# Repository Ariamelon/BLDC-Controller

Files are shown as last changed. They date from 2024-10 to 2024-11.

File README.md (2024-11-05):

# BLDC motor controller
A brushless DC motor controller developed in partial fulfilment of the requirements for a degree of BEng (Hons) Electronic & Computer Engineering.

## Disclaimer
The hardware is licensed under CERN-OHL-S-2.0, and the firmware is licensed under GNU GPLv3. 

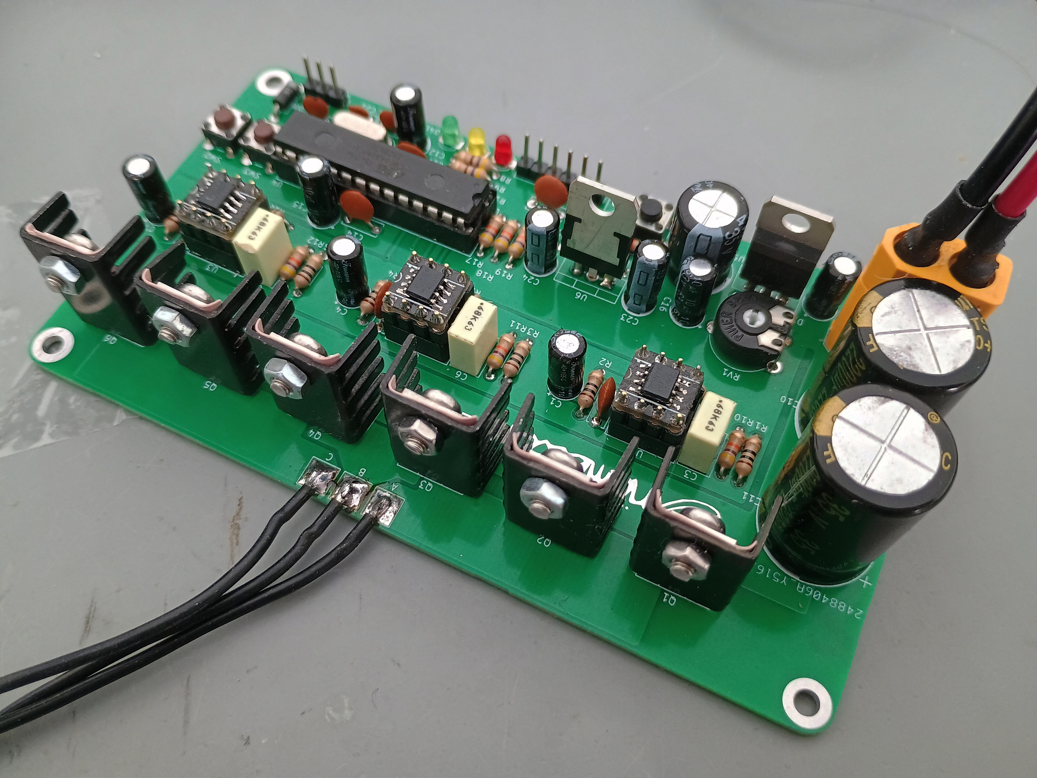
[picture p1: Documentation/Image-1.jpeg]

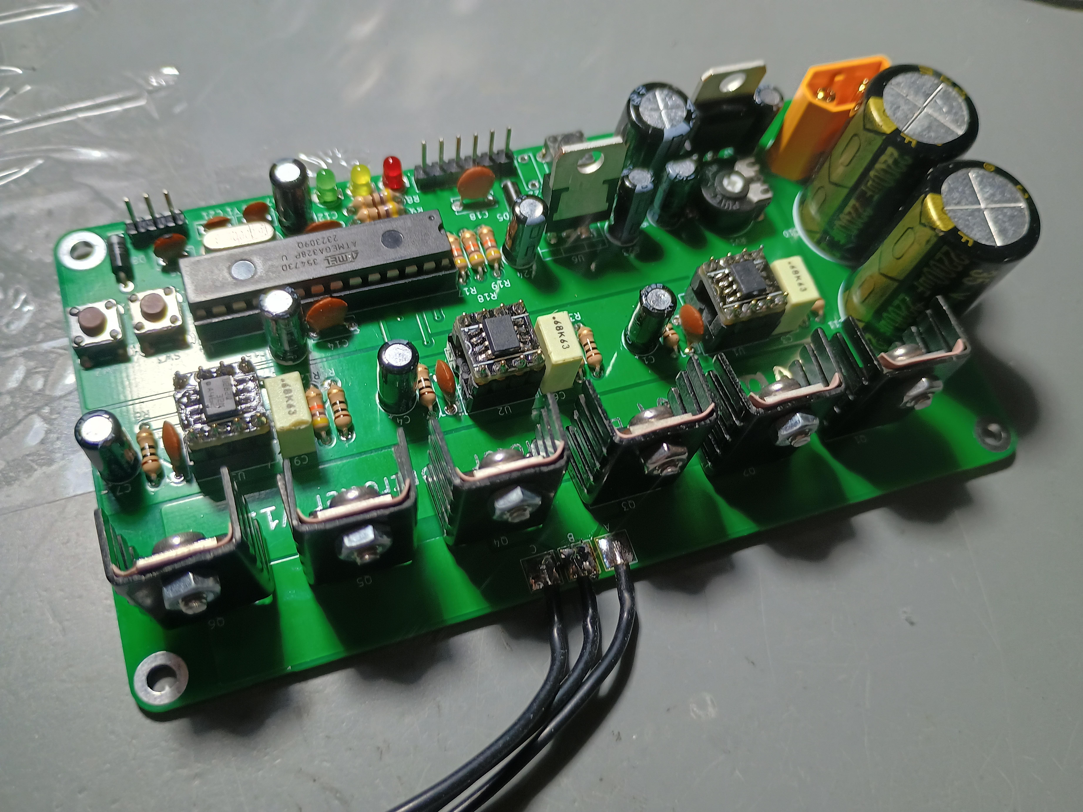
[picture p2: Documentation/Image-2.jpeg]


https://github.com/user-attachments/assets/5595b5e6-1121-481e-8a8e-658866d14e04

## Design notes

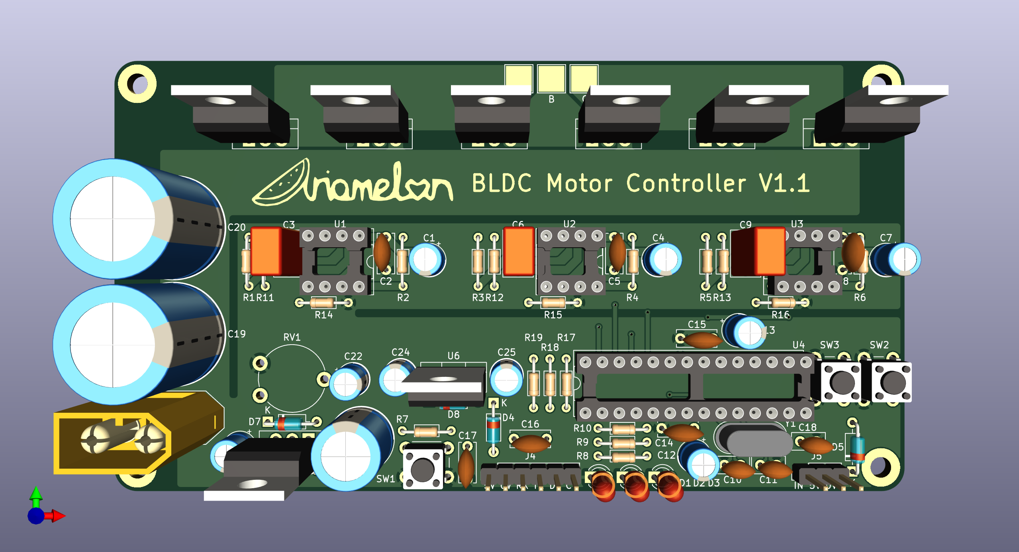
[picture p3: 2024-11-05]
Documentation/BLDC-Controller-3D.png

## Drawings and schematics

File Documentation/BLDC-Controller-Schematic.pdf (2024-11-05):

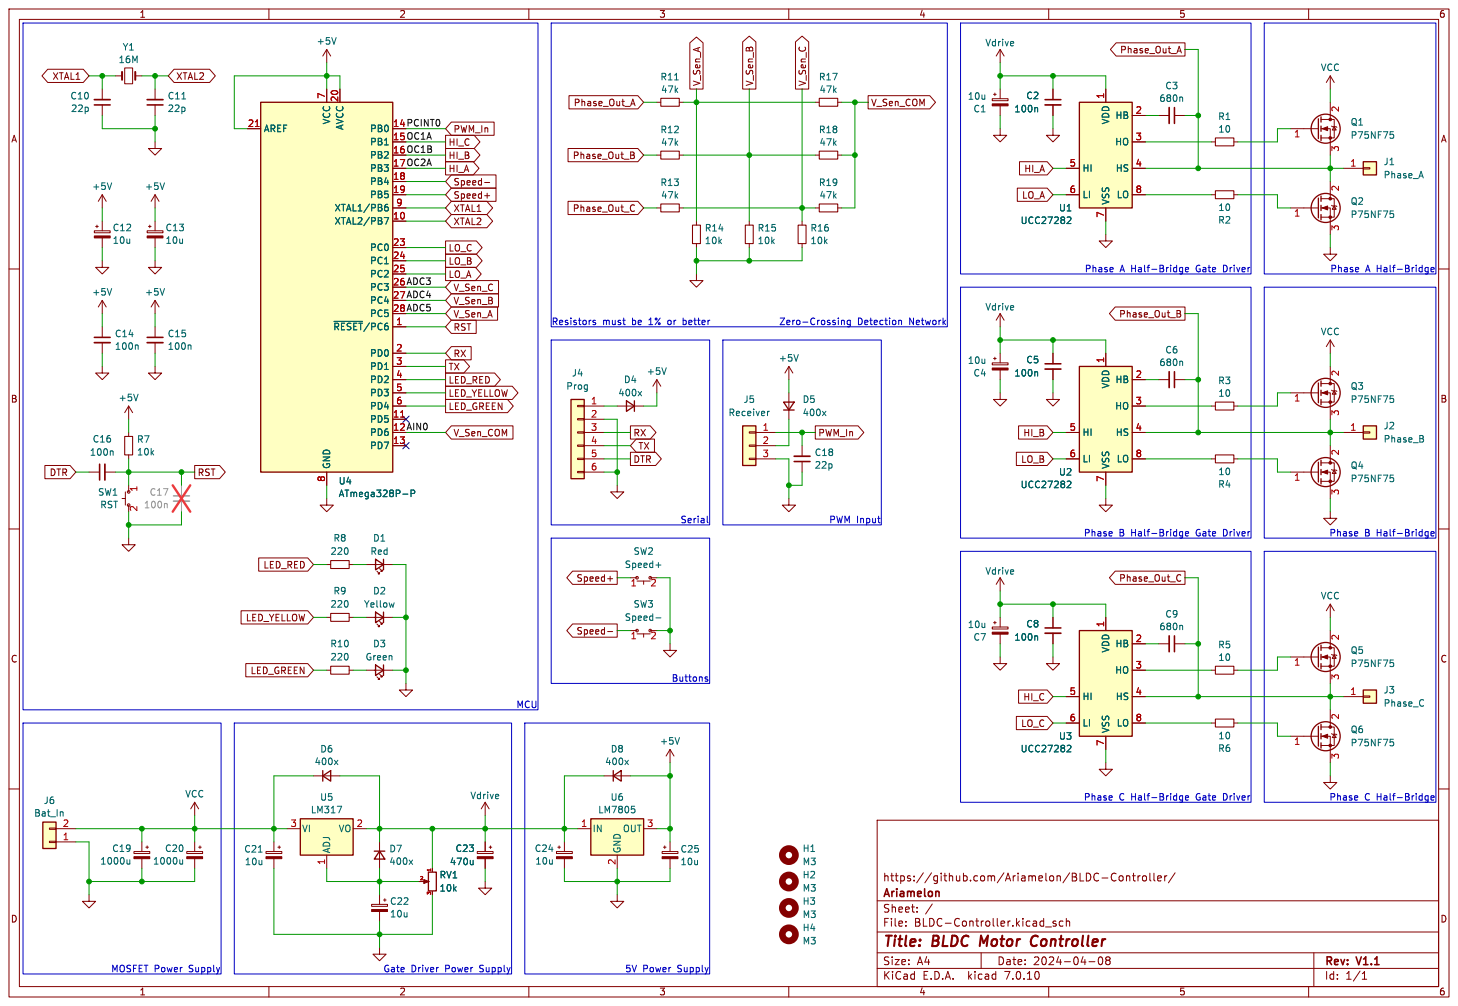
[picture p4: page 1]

https://github.com/Ariamelon/BLDC-Controller/
Id: 1/1 Title: BLDC Motor Controller File: BLDC-Controller.kicad_sch Sheet: / Ariamelon

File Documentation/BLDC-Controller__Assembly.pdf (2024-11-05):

# A CT C

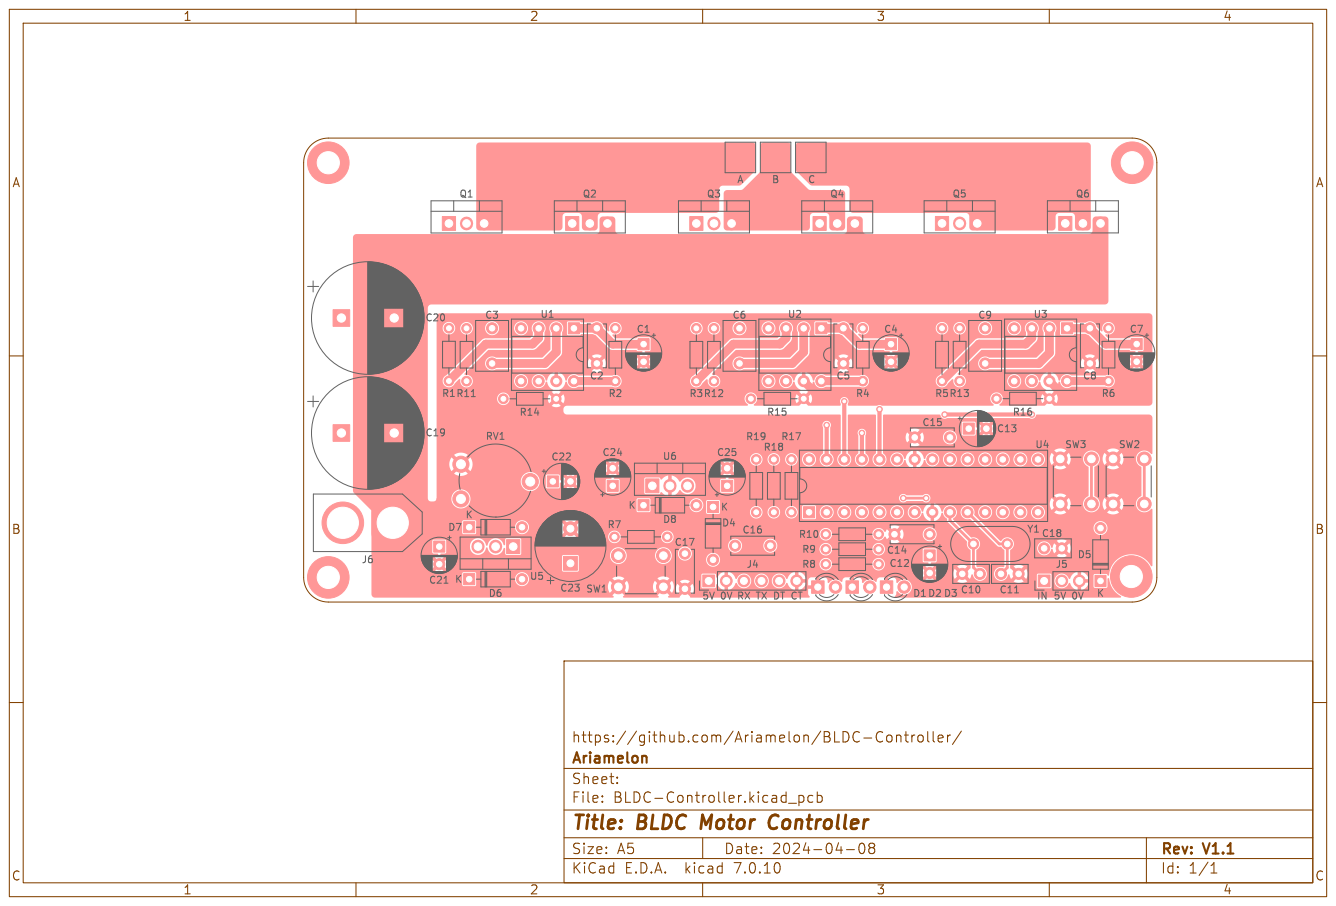
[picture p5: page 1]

https://github.com/Ariamelon/BLDC-Controller/

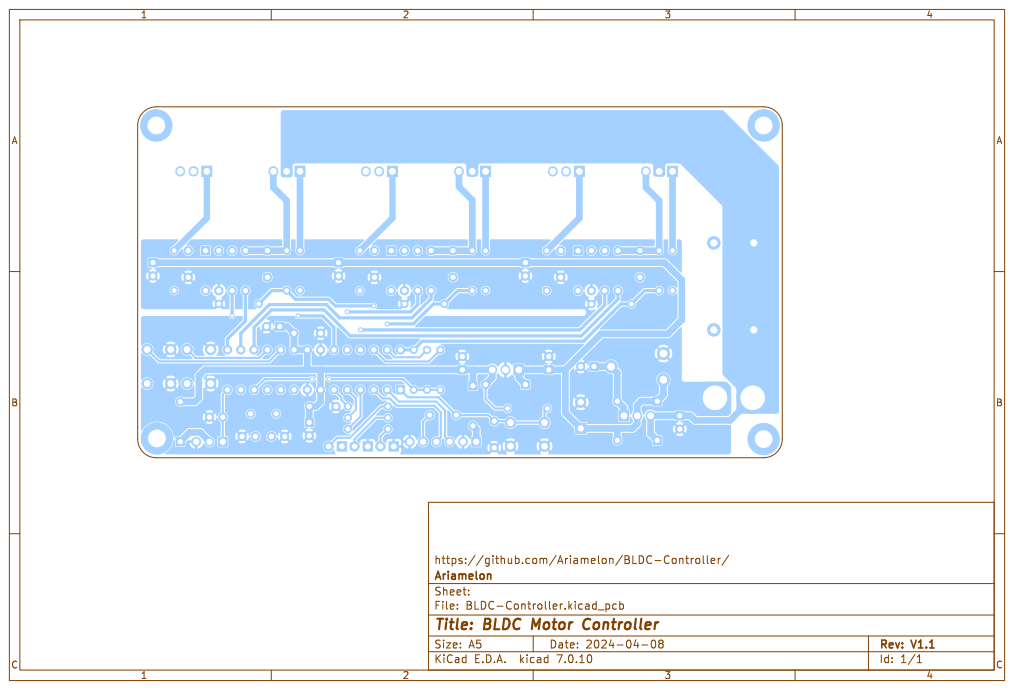
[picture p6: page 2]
BC Date: 2024-04-08 KiCad; kicad; 7.0.10 Size: A5; Rev: V1.1; Id: 1/1 Title: BLDC Motor Controller File:; BLDC-Controller.kicad_pcb Sheet: Ariamelon

https://github.com/Ariamelon/BLDC-Controller/

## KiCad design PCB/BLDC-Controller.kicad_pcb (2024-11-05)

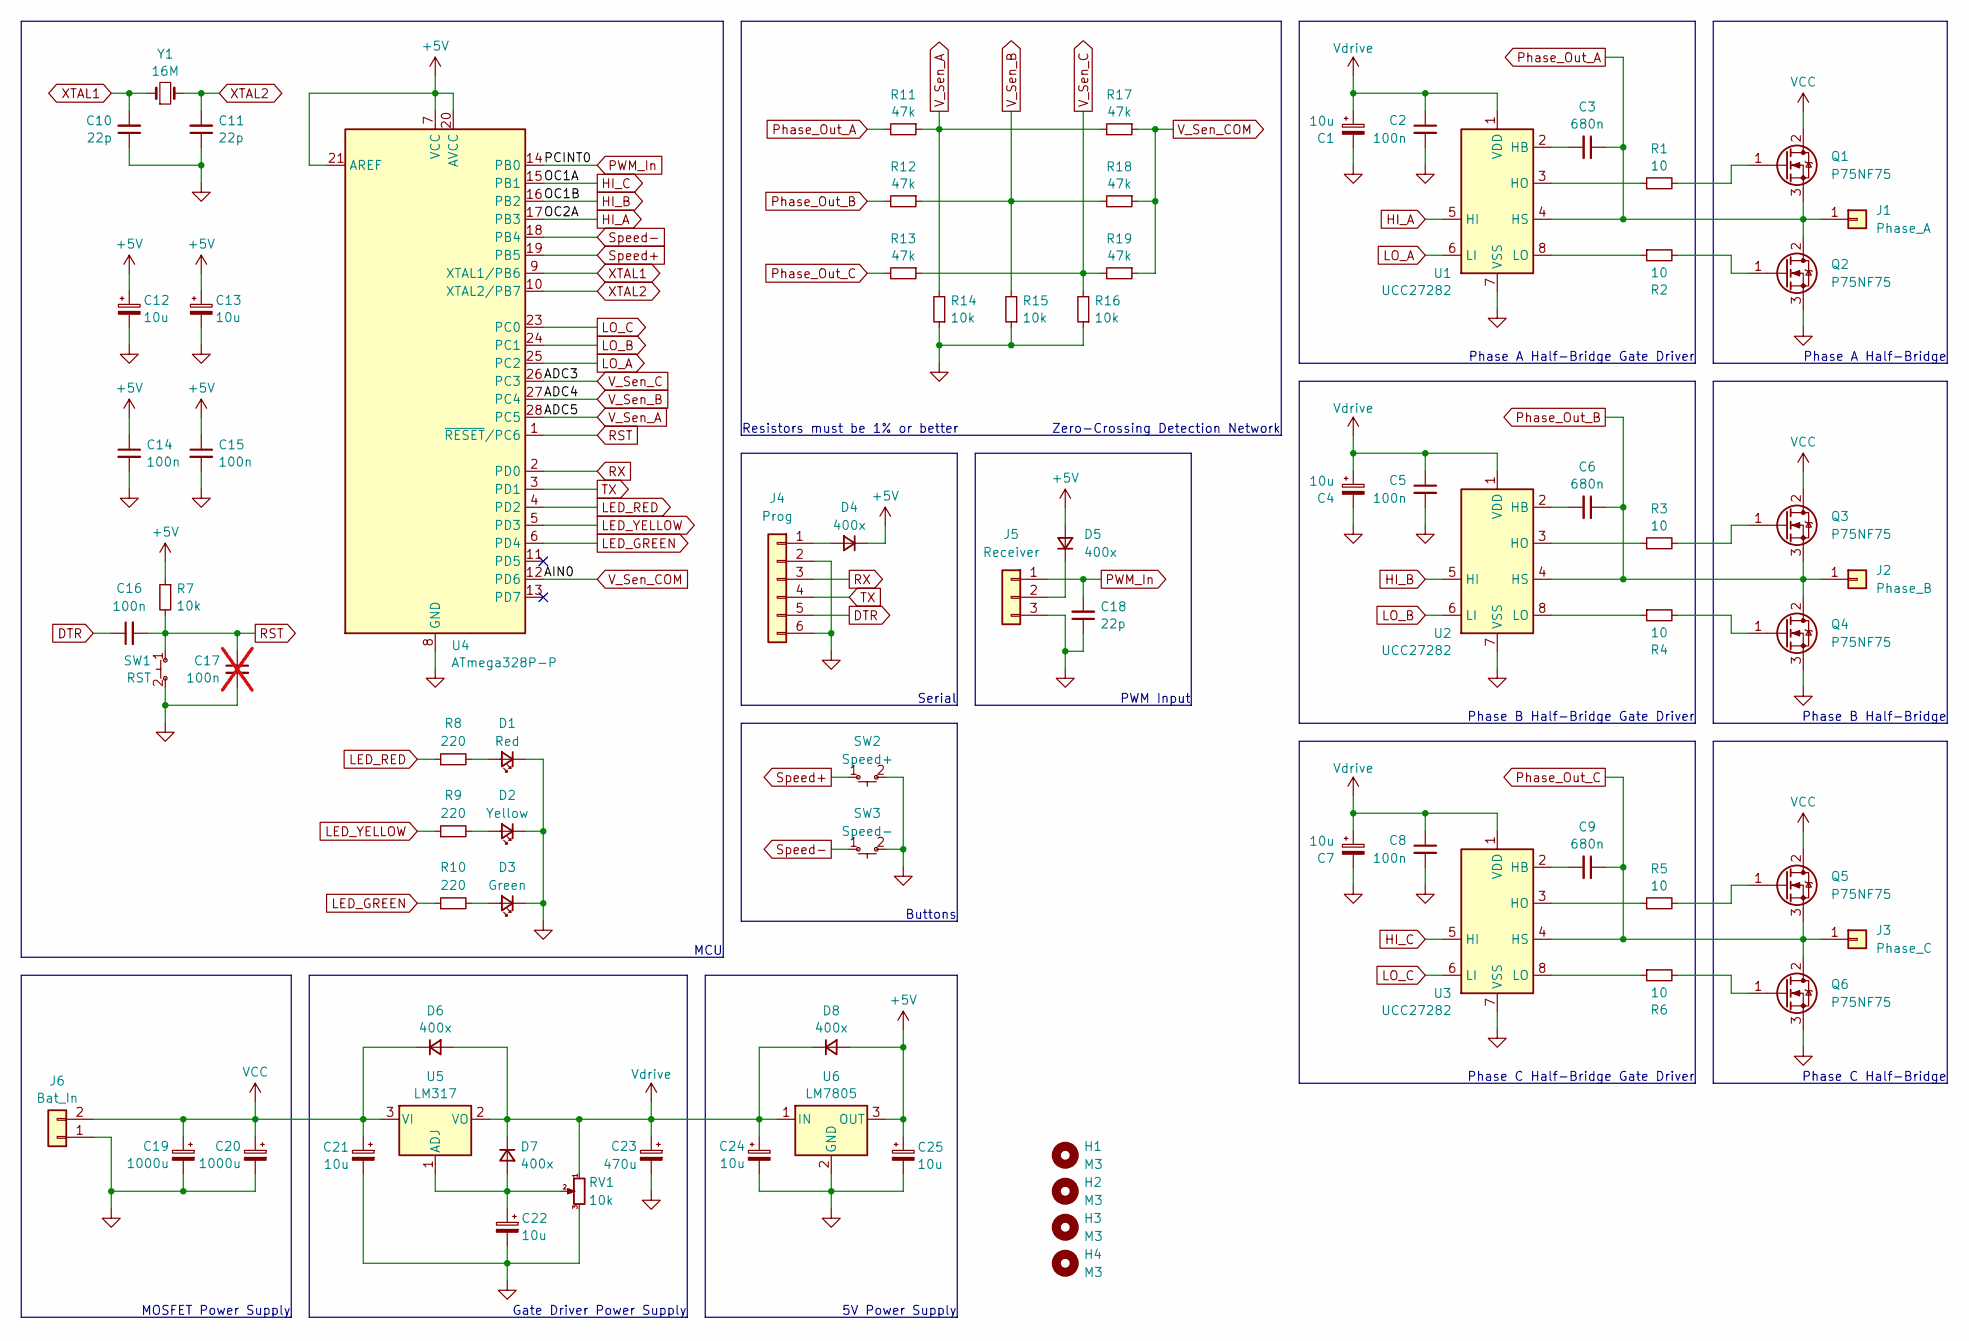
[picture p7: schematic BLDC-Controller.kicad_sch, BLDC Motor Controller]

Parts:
C1, C4, C7, C12, C13, C21, C22, C24, C25: 10u; CP_Radial_D5.0mm_P2.54mm
C2, C5, C8, C14, C15, C16: 100n; C_Disc_D6.0mm_W2.5mm_P5.08mm
C3, C6, C9: 680n; C_Rect_L7.0mm_W4.5mm_P5.08mm
C10, C11, C18: 22p; C_Disc_D5.0mm_W2.5mm_P2.54mm
C17: 100n; C_Disc_D6.0mm_W2.5mm_P5.08mm; not fitted
C19, C20: 1000u; CP_Radial_D16.0mm_P7.62mm
C23: 470u; CP_Radial_D10.0mm_P5.00mm
D1: Red; LED_D3.0mm
D2: Yellow; LED_D3.0mm
D3: Green; LED_D3.0mm
D4, D5, D6, D7, D8: 400x; D_DO-35_SOD27_P7.62mm_Horizontal
H1, H2, H3, H4: M3; MountingHole_3.2mm_M3_Pad
J1: Phase_A; TestPoint_Pad_4.0x4.0mm
J2: Phase_B; TestPoint_Pad_4.0x4.0mm
J3: Phase_C; TestPoint_Pad_4.0x4.0mm
J4: Prog; PinHeader_1x06_P2.54mm_Vertical
J5: Receiver; PinHeader_1x03_P2.54mm_Vertical
J6: Bat_In; AMASS_XT60-M_1x02_P7.20mm_Vertical
Q1, Q2, Q3, Q4, Q5, Q6: P75NF75; TO-220-3_Vertical
R1, R2, R3, R4, R5, R6: 10; R_Axial_DIN0204_L3.6mm_D1.6mm_P7.62mm_Horizontal
R7, R14, R15, R16: 10k; R_Axial_DIN0204_L3.6mm_D1.6mm_P7.62mm_Horizontal
R8, R9, R10: 220; R_Axial_DIN0204_L3.6mm_D1.6mm_P7.62mm_Horizontal
R11, R12, R13, R17, R18, R19: 47k; R_Axial_DIN0204_L3.6mm_D1.6mm_P7.62mm_Horizontal
RV1: 10k; Potentiometer_Piher_PT-10-V10_Vertical
SW1: RST; SW_PUSH_6mm
SW2: Speed+; SW_PUSH_6mm
SW3: Speed-; SW_PUSH_6mm
U1, U2, U3: UCC27282; DIP-8_W7.62mm_Socket
U4: ATmega328P-P; DIP-28_W7.62mm_Socket
U5: LM317; TO-220-3_Vertical
U6: LM7805; TO-220-3_Vertical
Y1: 16M; Crystal_HC49-4H_Vertical

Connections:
+5V: C12.1, C13.1, C14.1, C15.1, C25.1, D4.1 (K), D5.2 (A), D8.2 (A), R7.1, U4.7 (VCC), U4.20 (AVCC), U4.21 (AREF), U6.3 (OUT)
DTR: C16.1, J4.5
GND: C1.2, C2.2, C4.2, C5.2, C7.2, C8.2, C10.1, C11.1, C12.2, C13.2, C14.2, C15.2, C17.2, C18.1, C19.2, C20.2, C21.2, C22.2, C23.2, C24.2, C25.2, D1.1 (K), D2.1 (K), D3.1 (K), J4.2, J4.6, J5.3, J6.1, Q2.3 (S), Q4.3 (S), Q6.3 (S), R14.1, R15.1, R16.1, RV1.3, SW1.2 (B), SW2.2 (B), SW3.2 (B), U1.7 (VSS), U1.9 (EP), U2.7 (VSS), U2.9 (EP), U3.7 (VSS), U3.9 (EP), U4.8 (GND), U4.22 (GND), U6.2 (GND)
HI_A: U1.5 (HI), U4.17 (PB3)
HI_B: U2.5 (HI), U4.16 (PB2)
HI_C: U3.5 (HI), U4.15 (PB1)
LED_GREEN: R10.1, U4.6 (PD4)
LED_RED: R8.1, U4.4 (PD2)
LED_YELLOW: R9.1, U4.5 (PD3)
LO_A: U1.6 (LI), U4.25 (PC2)
LO_B: U2.6 (LI), U4.24 (PC1)
LO_C: U3.6 (LI), U4.23 (PC0)
unnamed: D1.2 (A), R8.2
unnamed: D2.2 (A), R9.2
unnamed: D3.2 (A), R10.2
unnamed: D4.2 (A), J4.1
unnamed: D5.1 (K), J5.2
unnamed: C22.1, D7.2 (A), RV1.2, U5.1 (ADJ)
unnamed: Q1.1 (G), R1.2
unnamed: Q2.1 (G), R2.2
unnamed: Q3.1 (G), R3.2
unnamed: Q4.1 (G), R4.2
unnamed: Q5.1 (G), R5.2
unnamed: Q6.1 (G), R6.2
unnamed: C3.2, U1.2 (HB)
unnamed: R1.1, U1.3 (HO)
unnamed: R2.1, U1.8 (LO)
unnamed: C6.2, U2.2 (HB)
unnamed: R3.1, U2.3 (HO)
unnamed: R4.1, U2.8 (LO)
unnamed: C9.2, U3.2 (HB)
unnamed: R5.1, U3.3 (HO)
unnamed: R6.1, U3.8 (LO)
PWM_In: C18.2, J5.1, U4.14 (PB0)
Phase_Out_A: C3.1, J1.1, Q1.3 (S), Q2.2 (D), R11.2, U1.4 (HS)
Phase_Out_B: C6.1, J2.1, Q3.3 (S), Q4.2 (D), R12.2, U2.4 (HS)
Phase_Out_C: C9.1, J3.1, Q5.3 (S), Q6.2 (D), R13.2, U3.4 (HS)
RST: C16.2, C17.1, R7.2, SW1.1 (A), U4.1 (~RESET/PC6)
RX: J4.3, U4.2 (PD0)
Speed+: SW2.1 (A), U4.19 (PB5)
Speed-: SW3.1 (A), U4.18 (PB4)
TX: J4.4, U4.3 (PD1)
VCC: C19.1, C20.1, C21.1, D6.1 (K), J6.2, Q1.2 (D), Q3.2 (D), Q5.2 (D), U5.3 (VI)
V_Sen_A: R11.1, R14.2, R17.2, U4.28 (PC5)
V_Sen_B: R12.1, R15.2, R18.2, U4.27 (PC4)
V_Sen_C: R13.1, R16.2, R19.2, U4.26 (PC3)
V_Sen_COM: R17.1, R18.1, R19.1, U4.12 (PD6)
Vdrive: C1.1, C2.1, C4.1, C5.1, C7.1, C8.1, C23.1, C24.1, D6.2 (A), D7.1 (K), D8.1 (K), RV1.1, U1.1 (VDD), U2.1 (VDD), U3.1 (VDD), U5.2 (VO), U6.1 (IN)
XTAL1: C10.2, U4.9 (XTAL1/PB6), Y1.1
XTAL2: C11.2, U4.10 (XTAL2/PB7), Y1.2

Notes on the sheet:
MOSFET Power Supply
Gate Driver Power Supply
Resistors must be 1% or better
5V Power Supply
PWM Input
Buttons
Phase A Half-Bridge Gate Driver
Serial
Zero-Crossing Detection Network
Phase C Half-Bridge Gate Driver
Phase C Half-Bridge
Phase A Half-Bridge
Phase B Half-Bridge
Phase B Half-Bridge Gate Driver
MCU

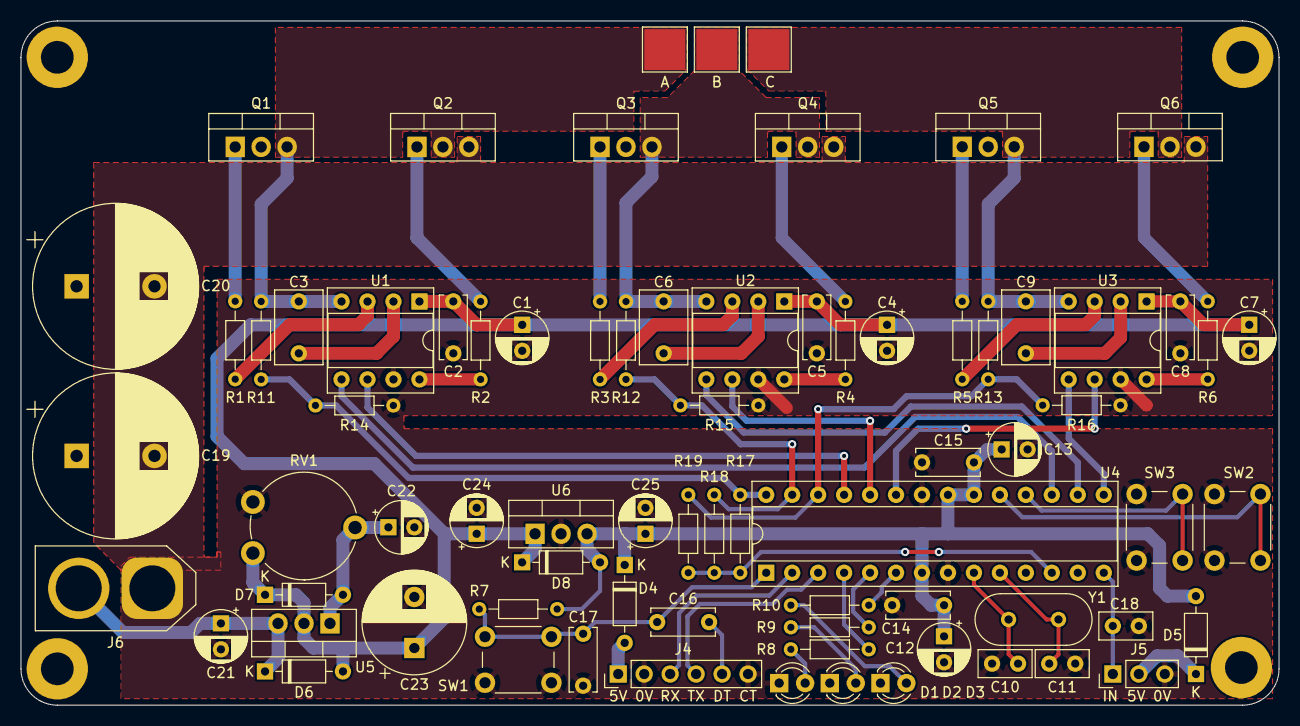
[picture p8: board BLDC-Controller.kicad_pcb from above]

Board: 2 copper layers, 123.1 x 66.9 mm, 80 parts (0 on the bottom side), 50 nets.

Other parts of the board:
A1: Art; Ariamelon_Logo_Large_Mask

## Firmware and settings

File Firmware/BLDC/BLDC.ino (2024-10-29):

/*
This file is part of BLDC control firmware.

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
You should have received a copy of the GNU General Public License along with BLDC control firmware.
If not, see <https://www.gnu.org/licenses/>. 
*/

#include <stdlib.h>
#include "Commutation.h"
#include "UART_Comms.h"

static volatile unsigned char commutation_step = 0;

// Analog comparator ISR
ISR (ANALOG_COMP_vect) {
  unsigned char i;

  // Debouncing filter. Reads values DEBOUNCE_PERIOD times before processing result.
  // Increases debounce period if BLDC step is odd & 0 detected on ACO (comparator output).
  // Or if BLDC step is even & 1 detected on ACO (comparator output).
  for(i = 0; i < DEBOUNCE_PERIOD; i++) {
    if(((commutation_step & 1) && !(ACSR & 0b00100000)) 
   || (!(commutation_step & 1) && (ACSR & 0b00100000))){
      i -= 1;
    }
  }

  commutation_step = commutation_step_set(commutation_step);
}

int main(void){
  init();
  
  Serial.begin(BAUD);
  while(Serial.available() > 0){
    Serial.read();
  }
  Serial.flush();
  
  Serial.println("Initializing BLDC motor controller.");
  initialize_controller();
  Serial.println("Initialization complete.");

  // Speed control via on-board buttons or serial input.
  // Some Arduino functions used here as speed is not critical.

  unsigned char pwm_old_duty = 0;
  unsigned char pwm_min_duty = 65 - VOLTAGE_IN * 2;
  int pwm_new_duty = 0;
  char uart_buffer[UART_BUFFER_SIZE];
  bool motor_spinning = 0;

  while(1){
    while(Serial.available() > 0){
      if(!UART_process_data(uart_buffer, UART_BUFFER_SIZE)){
        pwm_new_duty = strtoul(uart_buffer, NULL, 0);
      }
    }

    if(!(PINB & (1 << PINB5))){             // Speed up button pressed.
      pwm_new_duty++;
      delay(10);
    }

    else if(!(PINB & (1 << PINB4))){        // Speed down button pressed.
      pwm_new_duty--;
      delay(10);
    }

    if (pwm_new_duty < pwm_min_duty){
      if (pwm_new_duty > pwm_old_duty){     // Constrain lower limit.
        pwm_new_duty = pwm_min_duty;        // Interpret as motor start command.
      }
      else{
        pwm_new_duty = 0;                   // Interpret as motor stop command.
      }
    }
    else if (pwm_new_duty > PWM_MAX_DUTY){  // Constrain upper limit.
      pwm_new_duty = PWM_MAX_DUTY;
    }

    if (pwm_new_duty != pwm_old_duty){      // Ignore command if value is unchanged.
      if (pwm_new_duty == 0){
        motor_stop();
      }
      else if (pwm_old_duty == 0){          // If motor is stationary, any number starts the motor.
        pwm_new_duty = pwm_min_duty;
        commutation_step = motor_start(pwm_new_duty, commutation_step, VOLTAGE_IN);
      }
      Serial.print("Duty cycle: ");
      Serial.print(pwm_new_duty);
      Serial.println("/255.");

      pwm_duty_set(pwm_new_duty);
      pwm_old_duty = pwm_new_duty;
    }
  }  
}

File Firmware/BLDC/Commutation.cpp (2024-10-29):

/*
This file is part of BLDC control firmware.

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
You should have received a copy of the GNU General Public License along with BLDC control firmware.
If not, see <https://www.gnu.org/licenses/>. 
*/

#include "Arduino.h"
#include "Commutation.h"

void initialize_controller(void){
  DDRB   |= 0b00001110; // Configure HI_A (PB3), HI_B (PB2) and HI_C (PB1) (high side) as outputs.
  PORTB  &= 0b11110001; // Disable HI_A (PB3), HI_B (PB2) and HI_C (PB1).
  PORTB  |= 0b00110000; // Enable speed+ (PB5) and speed- (PB4) pullups.

  DDRC   |= 0b00000111; // Configure LO_A (PC2), LO_B (PC1) and LO_C (PC0) (low side) as outputs.
  PORTC  &= 0b11111000; // Disable LO_A (PC2), LO_B (PC1) and LO_C (PC0).
  
  DDRD   |= 0b00011100; // Configure red LED (PD2), yellow LED (PD3) and green LED (PD4) as outputs.
  PORTD  &= 0b11100111; // Disable yellow LED (PD3) and green LED (PD4).
  PORTD  |= 0b00000100; // Enable red LED (PD2).

  TCCR1A  = 0;          // Initialize timers 1 and 2.
  TCCR1B  = 0b00000001; // Clock source set to clkIO / 1 (no prescaling).
  TCCR2A  = 0;          // Allows for highest PWM frequency.
  TCCR2B  = 0b00000001; // Also disable PWM outputs.

  ACSR    = 0b00010000; // Disable and clear ACI flag (analog comparator interrupt).
  ADCSRA  = 0;          // Disable ADC.
}

unsigned char motor_start(unsigned char pwm_lowest_duty, unsigned char old_step, unsigned char input_voltage){
  Serial.print("Starting up motor. ");
  PORTD |= 0b00001000;  // Enable yellow LED (PD3).

  // Acceleration rate depends on duty cycle and input voltage.
  unsigned int delay_duration = OPEN_LOOP_DELAY;
  unsigned int delay_factor = 70;
  unsigned char pwm_start_duty = delay_factor - input_voltage;

  pwm_duty_set(pwm_start_duty);
  unsigned char new_step = old_step;

  new_step = commutation_step_set(new_step);  // Starts up motor even when rotor is still moving.
  delay(ALIGN_MS);

  // Open-loop commutation.
  pwm_duty_set(pwm_start_duty);
  while (delay_duration > 3000 / (input_voltage + 5)){
    new_step = commutation_step_set(new_step);
    delayMicroseconds(delay_duration);
    delay_duration -= delay_factor;
  }

  PORTD &= 0b11110111;  // Disable yellow LED (PD3).
  PORTD |= 0b00010000;  // Enable green LED (PD4).

  ACSR   = 0b00011000;  // Enable analog comparator interrupt and clear ACI flag.
  ADCSRB = 0b01000000;  // Enable analog comparator mux.
  return new_step;
}

void motor_stop(void){
  Serial.print("Shutting down motor. ");
  PORTD &= 0b11101111;  // Disable green LED (PD4).

  PORTC &= 0b11111000;  // Disable LO_A (PC2), LO_B (PC1) and LO_C (PC0).

  TCCR1A = 0;           // Disable HI_C (0C1A) and HI_B (OC1B).
  TCCR2A = 0;           // Disable HI_A (OC2A).

  ADCSRB = 0;           // Disable analog comparator mux.
  ACSR   = 0b00010000;  // Disable analog comparator interrupt and clear analog comparator interrupt flag.
}

unsigned char commutation_step_set(unsigned char current_step){ // BLDC motor commutation function.
  switch(current_step){
    case 0:
      PORTC &= 0b11111010;  // Disable LO_A (PC2) and LO_C (PC0).
      PORTC |= 0b00000010;  // Enable LO_B (PC1).

      TCCR1A = 0;           // Disable HI_C (0C1A) and HI_B (OC1B).
      TCCR2A = 0b10000001;  // Enable HI_A (OC2A) in PWM, phase correct, 8-bit mode.

      ADMUX  = 0b00000011;  // Select V_Sen_C (ADC3) as comparator inverting input.
      ACSR  |= 0b00000011;  // Set interrupt on rising edge.
      break;
    case 1:
      PORTC &= 0b11111001;  // Disable LO_A (PC2) and LO_B (PC1).
      PORTC |= 0b00000001;  // Enable LO_C (PC0).

      TCCR1A = 0;           // Disable HI_C (0C1A) and HI_B (OC1B).
      TCCR2A = 0b10000001;  // Enable HI_A (OC2A) in PWM, phase correct, 8-bit mode.

      ADMUX  = 0b00000100;  // Select V_Sen_B (ADC4) as comparator inverting input.
      ACSR  &= 0b11111110;  // Set interrupt on falling edge.
      break;
    case 2:
      PORTC &= 0b11111001;  // Disable LO_A (PC2) and LO_B (PC1).
      PORTC |= 0b00000001;  // Enable LO_C (PC0).

      TCCR2A = 0;           // Disable HI_A (OC2A).
      TCCR1A = 0b00100001;  // Enable HI_B (OC1B) in PWM, phase correct, 8-bit mode and disable HI_C (0C1A).
      
      ADMUX  = 0b00000101;  // Select V_Sen_A (PC5) as comparator inverting input.
      ACSR  |= 0b00000011;  // Set interrupt on rising edge.
      break;
    case 3:
      PORTC &= 0b11111100;  // Disable LO_B (PC1) and LO_C (PC0).
      PORTC |= 0b00000100;  // Enable LO_A (PC2).

      TCCR2A = 0;           // Disable HI_A (OC2A).
      TCCR1A = 0b00100001;  // Enable HI_B (OC1B) in PWM, phase correct, 8-bit mode and disable HI_C (0C1A).
      
      ADMUX  = 0b00000011;  // Select V_Sen_C (ADC3) as comparator inverting input.
      ACSR  &= 0b11111110;  // Set interrupt on falling edge.
      break;
    case 4:
      PORTC &= 0b11111100;  // Disable LO_B (PC1) and LO_C (PC0).
      PORTC |= 0b00000100;  // Enable LO_A (PC2).

      TCCR2A = 0;           // Disable HI_A (OC2A).
      TCCR1A = 0b10000001;  // Enable HI_C (0C1A) in PWM, phase correct, 8-bit mode and disable HI_B (OC1B).
      
      ADMUX  = 0b00000100;  // Select V_Sen_B (ADC4) as comparator inverting input.
      ACSR  |= 0b00000011;  // Set interrupt on rising edge.
      break;
    case 5:
      PORTC &= 0b11111010;  // Disable LO_A (PC2) and LO_C (PC0).
      PORTC |= 0b00000010;  // Enable LO_B (PC1).

      TCCR2A = 0;           // Disable HI_A (OC2A).
      TCCR1A = 0b10000001;  // Enable HI_C (0C1A) in PWM, phase correct, 8-bit mode and disable HI_B (OC1B).
            
      ADMUX  = 0b00000101;  // Select V_Sen_A (PC5) as comparator inverting input.
      ACSR  &= 0b11111110;  // Set interrupt on falling edge.
      break;
  }
  unsigned char next_step = current_step + 1;
  next_step %= 6;
  return next_step;
}

void pwm_duty_set(unsigned char duty){
  OCR1A = OCR1B = OCR2A = duty; // Set PWM duty cycle for all outputs.
}

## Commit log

2024-02-13 Completed initial prototype.
    [BLDC-Controller.kicad_pcb, BLDC-Controller.kicad_sch, MCU.kicad_sch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]
2024-02-19 Fixed pin assignment. Added tentative arduino code.
    [BLDC-Controller.kicad_pcb, MCU.kicad_sch, Phase.kicad_sch]
2024-03-09 Uploaded working software.
    [BLDC-Controller.kicad_pcb, BLDC-Controller.kicad_sch, Phase.kicad_sch]
2024-03-13 Updated to V1.1. Removed extra parts. Rearranged components.
    [BLDC-Controller.kicad_pcb, BLDC-Controller.kicad_sch, MCU.kicad_sch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]
2024-03-13 Updated to V1.1. Removed extra parts. Rearranged components. Added on-board LEDs.
    [BLDC-Controller.kicad_pcb, BLDC-Controller.kicad_sch, MCU.kicad_sch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]
2024-03-14 Updated PCB for better grounding.
    [BLDC-Controller.kicad_pcb]
2024-03-24 Updated firmware.
    [BLDC-Controller.kicad_pcb, MCU.kicad_sch]
2024-04-09 Fixed issues with code. Updated schematic.
    [BLDC-Controller.kicad_pcb, BLDC-Controller.kicad_sch, MCU.kicad_sch]
2024-04-10 Uploaded images on system operation. Updated schematic.
    [BLDC-Controller.kicad_pcb, BLDC-Controller.kicad_sch, MCU.kicad_sch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]
2024-04-10 Updated schematic.
    [BLDC-Controller.kicad_sch]
2024-05-05 Updated schematic. Added new documentation.
    [BLDC-Controller.kicad_sch]
2024-05-18 Added new images. Modified schematic and PCB.
    [BLDC-Controller.kicad_pcb, BLDC-Controller.kicad_sch]
2024-05-20 Final update before project completion.
    [BLDC-Controller.kicad_pcb]
2024-11-05 Removed extraneous details.
    [BLDC-Controller.kicad_pcb, BLDC-Controller.kicad_sch]

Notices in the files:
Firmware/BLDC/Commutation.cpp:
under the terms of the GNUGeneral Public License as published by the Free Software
